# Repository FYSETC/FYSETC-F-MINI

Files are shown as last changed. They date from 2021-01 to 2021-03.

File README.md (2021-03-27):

# F-MINI

This is our open source machine: F-mini. Welcome to give us suggestions. We will keep updating this machine. You can open `F-MINI.step` file to have a 3D view. 

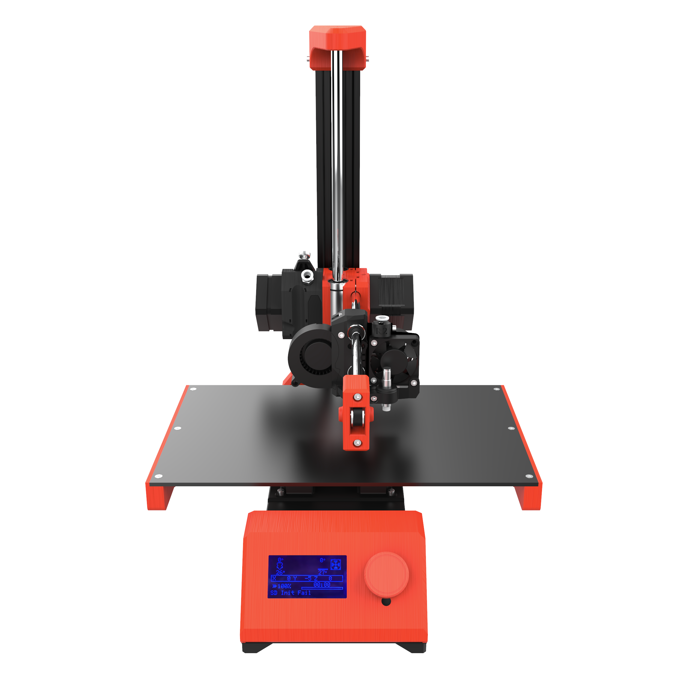
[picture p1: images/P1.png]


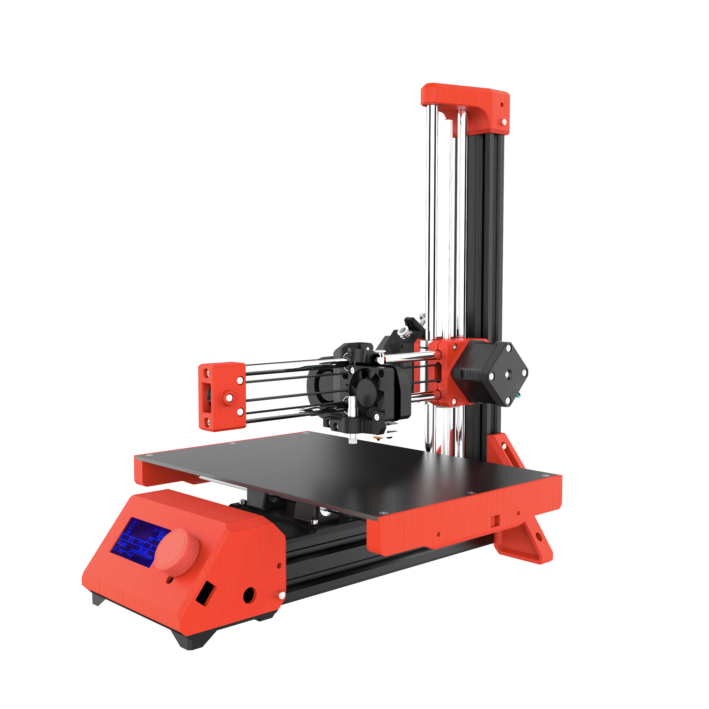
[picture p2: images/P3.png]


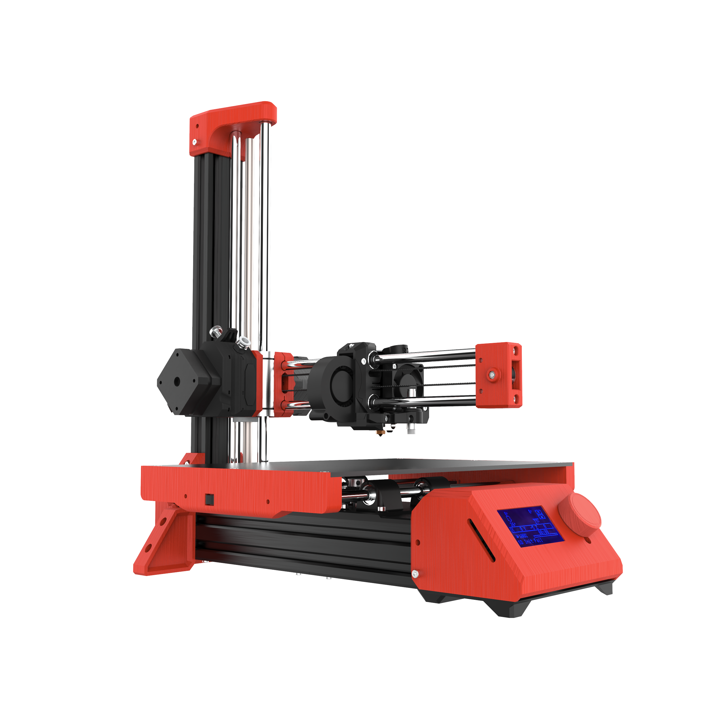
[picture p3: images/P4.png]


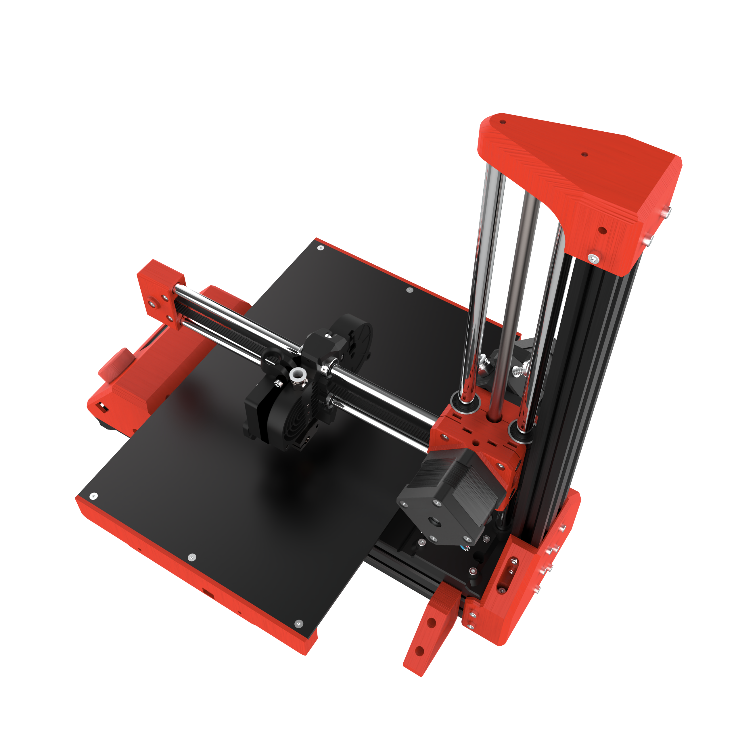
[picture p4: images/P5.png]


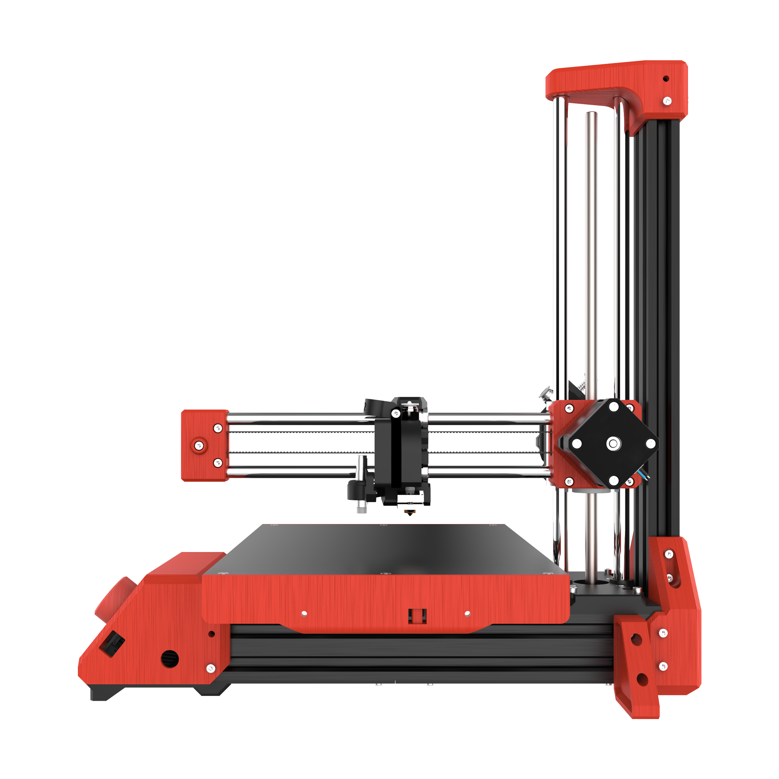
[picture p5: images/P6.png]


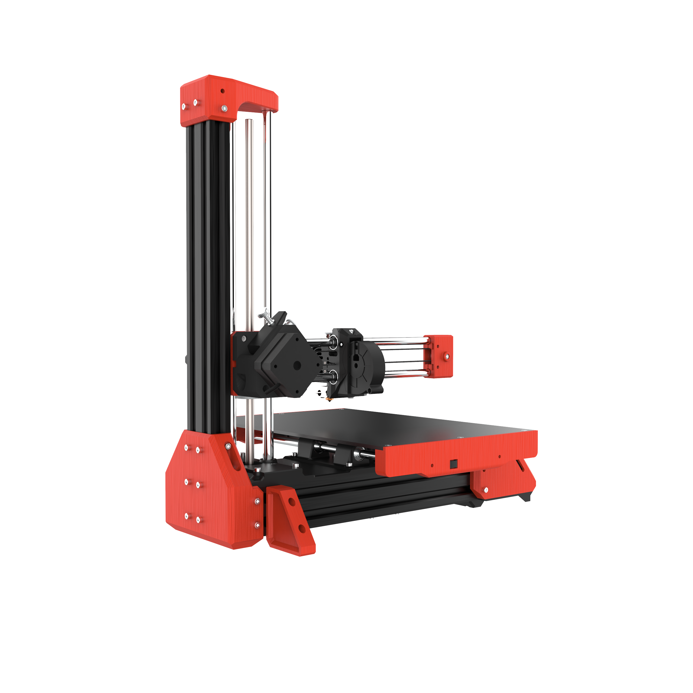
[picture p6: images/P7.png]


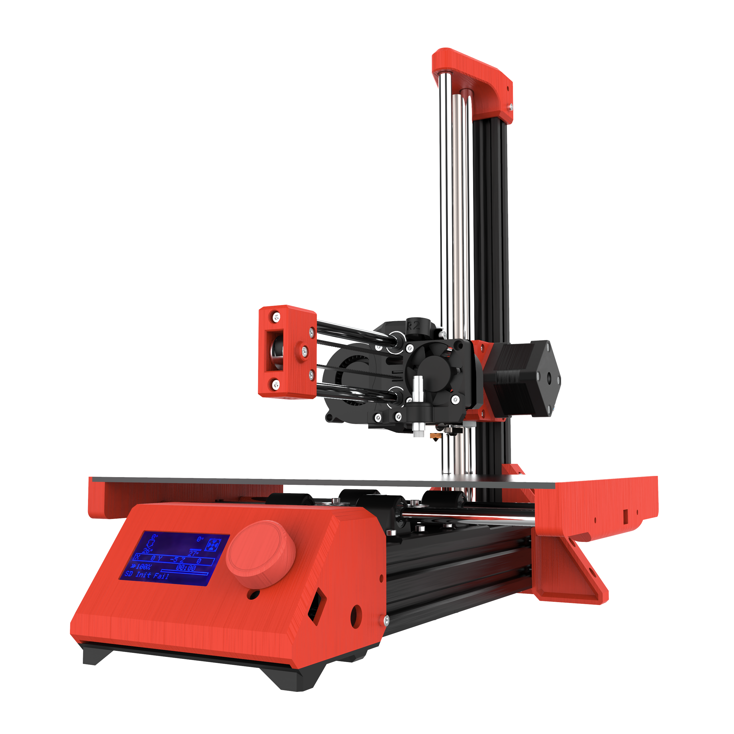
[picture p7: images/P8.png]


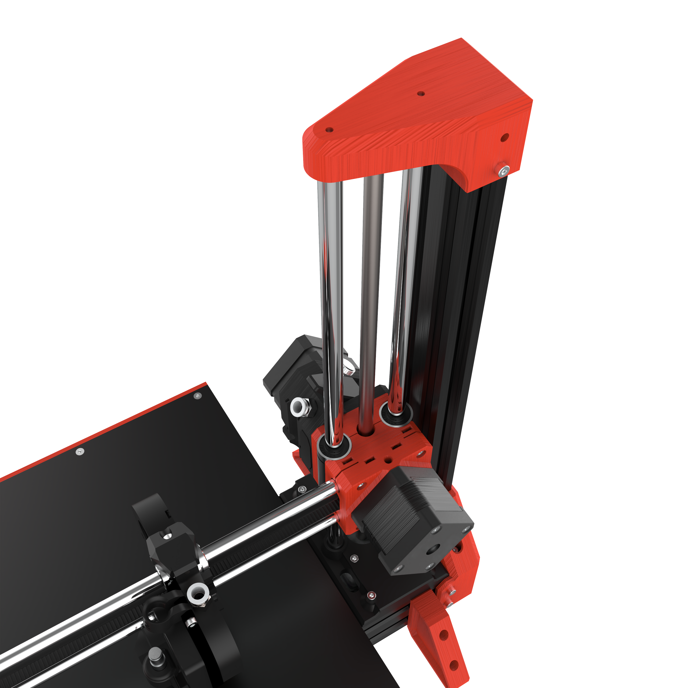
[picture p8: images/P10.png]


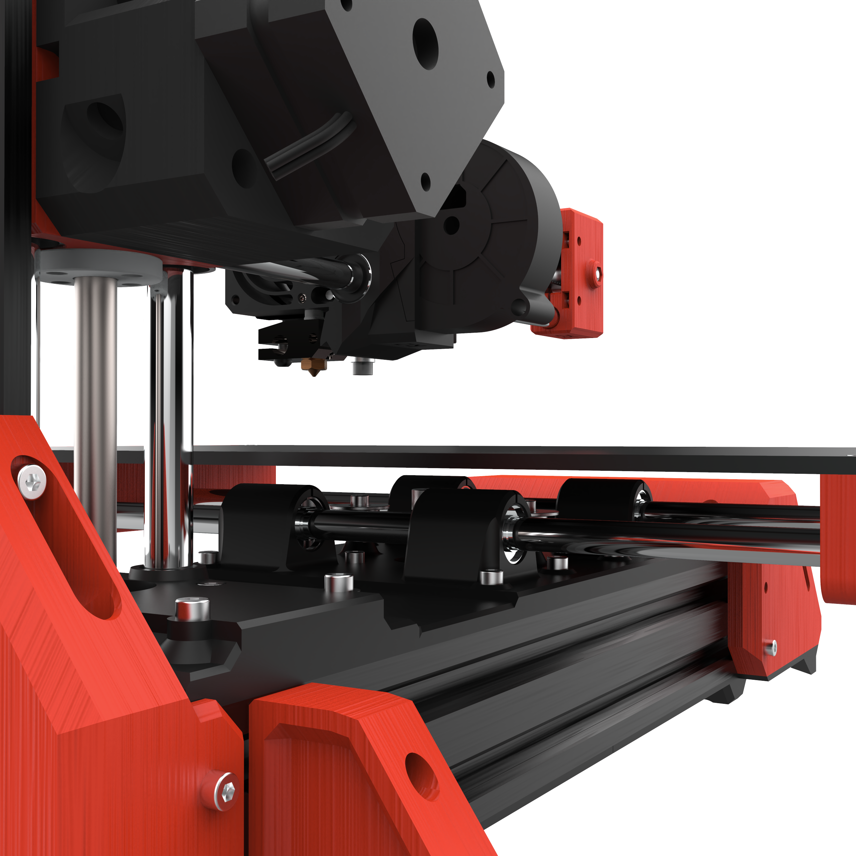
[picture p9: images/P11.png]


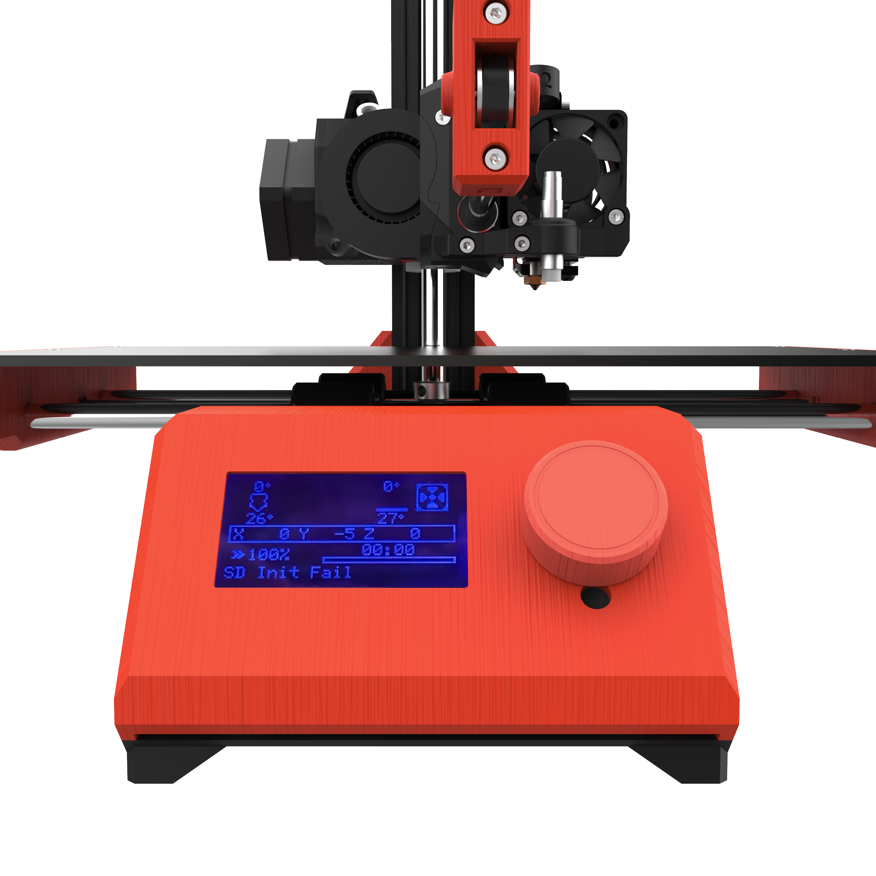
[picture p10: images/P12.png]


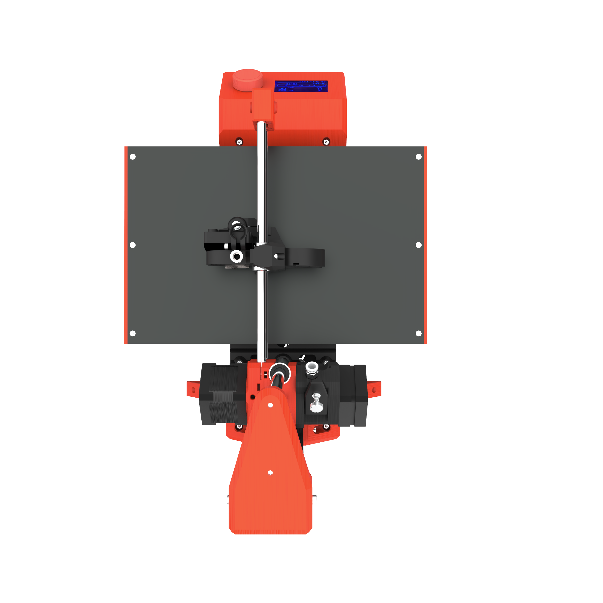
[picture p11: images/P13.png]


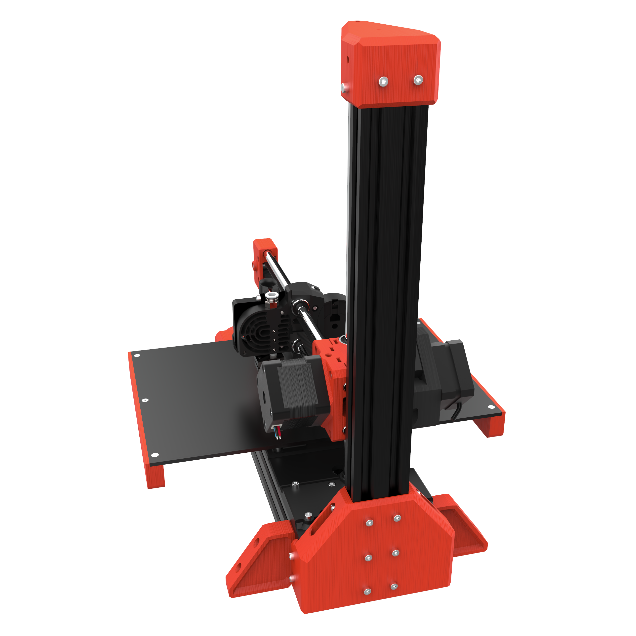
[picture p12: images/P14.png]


## Firmware

Firmware is in the `firmware` folder. Follow the `README.md` there. 

## Installation

Please follow the `installation.md` .

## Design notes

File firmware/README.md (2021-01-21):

# Firmware guide

F-MINI build with [FYSETC-AIO_II](https://github.com/FYSETC/FYSETC-AIO_II) motherboard using `Marlin` firmware.

## Marlin

### Pre-buids

There is `firmware.hex` pre-build firmware for you to test the board if you can't drive F-MINI with your own firmware.

### Build the firmware

You can follow the following steps to build the firmware your self.

#### Download Vscode + platformio

To compile the firmware , you need to install Visual Studio Code and the platformio pulg-in.

#### Download firmware

If you download already downloaded this repo, the firmware is in the ```firmware``` folder.

#### Configure the firmware

If you don't change anything of the machine, you don't need to change the configuration.

#### Compile the firmware

Open Vscode and open platformio main page and click the "Open Project" button , and direct to the folder where you put your firmware.

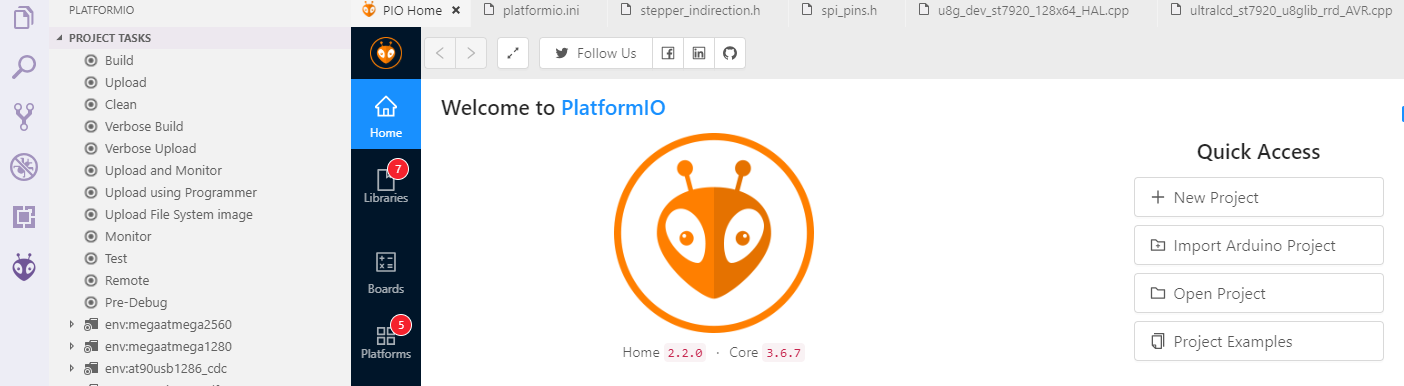
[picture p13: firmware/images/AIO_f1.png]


If everything goes fine , at the bottom you can see several buttons



Then click check mark to compile.

If you can't generate the hex file, you may need to open vscode using Administrator Account .

For more detail information，you can refer to http://marlinfw.org/docs/basics/install_platformio.html

#### Upload the firmware(windows,linux,Mac)

We provide several ways to upload the firmware .You can just click the upload button to upload the firmware or refer to the two methods below.

#### Upload the firmware(windows)

After compiling , you should see the firmware file "firmware.hex" in the folder FIRMWARE_LOCATE\Marlin\Marlin\\.pioenvs\fysetc_STM32F1\

Download the flash software in our github https://github.com/FYSETC/STM32Flasher

Connect the board and your pc with USB cable (This step should before you open the software)

Double the click "FlyMcu.exe" software to open it.

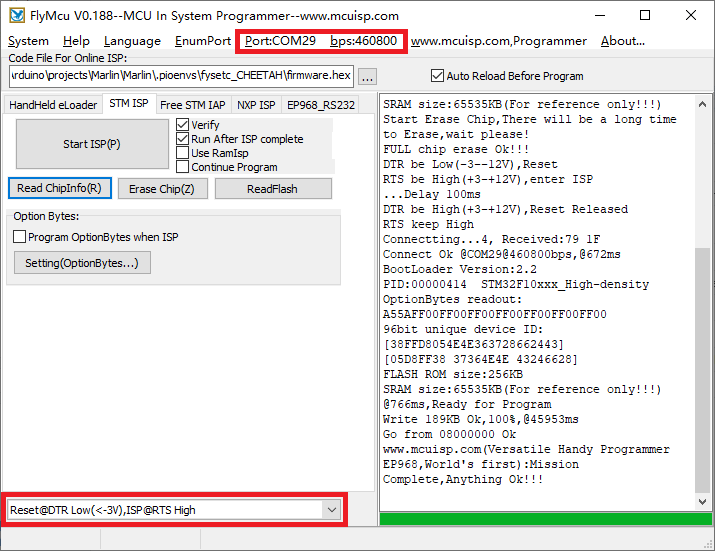
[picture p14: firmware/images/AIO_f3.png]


1. Select "***Reset@DTR low(<-3v),ISP @RTS High***"
2. Click "Port" to select the port of your USB 
3. Select ***FIRMWARE_LOCATE\Marlin\Marlin\\.pioenvs\fysetc_STM32F1\firmware.hex*** as the screenshot shows.
4. At last ,click the "Start ISP(p)" to upload the firmware.

#### Upload the firmware(linux)

##### Load usb driver

Delete the old version driver /lib/modules/$(uname -r)/kernel/drivers/usb/serial/ch341.ko

```
rm /lib/modules/$(uname -r)/kernel/drivers/usb/serial/ch341.ko
```

Download the CH34x driver(linux version) from our github

https://github.com/FYSETC/CH340-Driver

follow the readme.txt to make and load the driver .

If you want the driver load automatically every time your PC power up. You can copy the ch34x.ko file to 

directory /lib/modules/$(uname -r)/kernel/drivers/usb/serial/ , and do

```
depmod 
```

##### Install stm32flash tool

First get the code

```
git clone https://git.code.sf.net/p/stm32flash/code stm32flash-code
```

Then follow the INSTALL file to install the software

##### Upload the firmware

Connect the motherboard with USB cable and your PC. And do

```
dmesg
```

And you will get message like 



the ttyUSB0 is the port to communicate with the motherboard.

And then go the the firmware.hex file location directory and do the follow command to upload the firmware

```
 stm32flash -w firmware.hex -v -i rts,-dtr /dev/ttyUSB0
```

## Bootloader

If you want to update the firmware from sdcard, you can try this [bootloader.](https://github.com/FYSETC/Bootloader-STM32F103) Follow the README there. Or use the pre-build one in ```bootloader``` folder besides this README.

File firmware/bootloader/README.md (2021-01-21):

# Bootloader guide

You can use the sdcard to update the firmware for FYSETC-AIO_II board, you need to follow the following steps.

## Upload bootloader

You can use the bootloader hex you build or use the pre-build hex file in the OUTPUT folder.

You can use SWD , serial or USB cable. And if you are using our [Cheetah](https://github.com/FYSETC/FYSETC-Cheetah) or [AIO_II](https://github.com/FYSETC/FYSETC-AIO_II) boards , you can upload it with the STM32Flasher software which only work in Windows.

### Option 1: Upload the bootloader(windows)

There is bootloader file name ```Bootloader-STM32F103.hex``` beside this README file.

Download the flash software in our github https://github.com/FYSETC/STM32Flasher

Power the board with power supply and connect the board to your PC with USB cable (This step should before you open the software)

Double the click "FlyMcu.exe" software and open ```Bootloader-STM32F103.hex``` file.

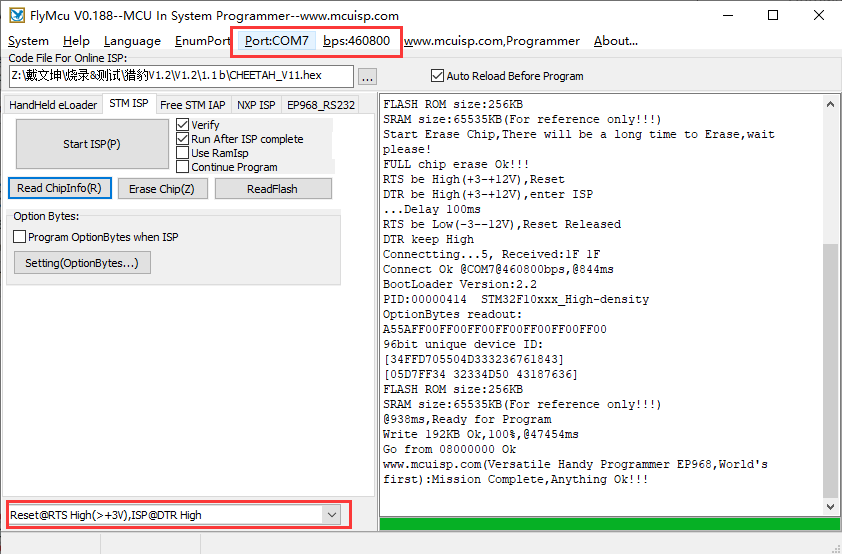
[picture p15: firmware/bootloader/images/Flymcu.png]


Select "Reset@DTR low(<-3v),ISP @RTS High"

Click "Port" to select the port of your USB 

Open Bootloader-STM32F103.hex file in the ''Code File For Online ISP:'' Editbox.

At last , "Start ISP(p)" to upload the firmware.

### Option2 : Upload the bootloader(linux)

#### Load usb driver

Delete the old version driver /lib/modules/$(uname -r)/kernel/drivers/usb/serial/ch341.ko

```
rm /lib/modules/$(uname -r)/kernel/drivers/usb/serial/ch341.ko
```

Download the CH34x driver(linux version) from our github

https://github.com/FYSETC/CH340-Driver

follow the readme.txt to make and load the driver .

If you want the driver load automatically every time your PC power up. You can copy the ch34x.ko file to 

directory /lib/modules/$(uname -r)/kernel/drivers/usb/serial/ , and do

```
depmod 
```

#### Install stm32flash tool

First get the code

```
git clone https://git.code.sf.net/p/stm32flash/code stm32flash-code
```

Then follow the INSTALL file to install the software

#### Upload the bootloader

Connect the motherboard with USB cable and your PC. And do

```
dmesg
```

And you will get message like 



the ttyUSB0 is the port to communicate with the motherboard.

And then go the the firmware.hex file location directory and do the follow command to upload the firmware

```
 stm32flash -w Bootloader-STM32F103.hex -v -i rts,-dtr /dev/ttyUSB0
```

## Rebuild firmware(Marlin)

This bootloader default boot address is 0x8010000 , so if you want to use this bootloader you need to change the firmware(I think you use Marlin, also you can use other firmware) flash address to 0x8010000.

And if you are using our stm32f103 boards([AIO_II](https://github.com/FYSETC/FYSETC-AIO_II) or [Cheetah](https://github.com/FYSETC/FYSETC-Cheetah)) . You need to add the following lines to the file "Marlin\Marlin\buildroot\share\PlatformIO\scripts\fysetc_STM32F1.py" (or check Marlin PR: https://github.com/MarlinFirmware/Marlin/pull/18179)

```
# Relocate firmware from 0x08000000 to 0x08010000
for define in env['CPPDEFINES']:
    if define[0] == "VECT_TAB_ADDR":
        env['CPPDEFINES'].remove(define)
env['CPPDEFINES'].append(("VECT_TAB_ADDR", "0x08010000"))

custom_ld_script = os.path.abspath("buildroot/share/PlatformIO/ldscripts/fysetc_stm32f103rc.ld")
for i, flag in enumerate(env["LINKFLAGS"]):
    if "-Wl,-T" in flag:
        env["LINKFLAGS"][i] = "-Wl,-T" + custom_ld_script
    elif flag == "-T":
        env["LINKFLAGS"][i + 1] = custom_ld_script
```

You can add it after the line 

```
Import("env")
```

And then rebuild the 3d printer firmware.

## Upload firmware(Marlin) with sdcard

After you upload the bootloader and rebuild the firmware(Marlin), now you can upload it to the board with sdcard

1. Copy the firmware(Marlin) to the SD card , you need to be sure the firmware name is "firmware.bin". 
2. And then power off the machine.
3. Insert the SD card to the board.
4. Power on the machine. 
5. And wait for 10~30 seconds , it will be done. 

You can connect the usb cable to monitor the process.

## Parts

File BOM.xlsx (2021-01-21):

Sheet: small 中文
模块部件 | 名称 | 规格 | 数量 | 单位 | 备注 | 参考图片 | 参考链接 | 所需紧固件明细 | 数量 | 红色备注表示已有物料
X轴模块 | X轴光轴 | 光轴直径8mm，长279mm，两端铣平，倒角C0.5 | 2 | pcs | MINI-X轴光轴 |  |  | 圆柱头内六角M3×12 | 16
 | 直线轴承 | 直线轴承LM8UU 内径8mm 外径15 高24mm 不生锈 | 2 | pcs |  |  | https://de.aliexpress.com/item/32849944212.html?spm=a2g0x.12010612.8148356.15.1f834918BBmogy | M3六角螺母 | 8
 | 直线轴承 | 直线轴承LM10LUU 内径10mm 外径19mm 高55mm 不生锈 | 2 | pcs |  |  | https://de.aliexpress.com/item/32849944212.html?spm=a2g0x.12010612.8148356.15.1f834918BBmogy | 圆柱头内六角半牙M3×25 | 6
 | 从动轮 | 20齿，内径3mm，外径12mm，高9mm，法兰厚1mm，直径18mm | 1 | pcs | 带宽6 20齿 内孔3 |  |  | M3锁紧螺母 | 2
 | 塑料卡爪 | 黑色卡爪固定4MM管 | 1 |  | miniBMG V1 |  | https://de.aliexpress.com/item/4001244491254.html | M3方形螺母 | 15
 | 卡爪夹片 | 4mm卡爪夹片 卡扣 | 1 |  |  |  |  | 圆柱头内六角半牙M3×40 | 1
 | 齿轮1.75 带机米 | 1.75-5-14-12-13.5 bondtech Gear 机米M3x2 | 1 |  |  |  |  | 圆柱头内六角半牙M3×30 | 4
 | 齿轮1.75 不带机米 | 1.75-5-14-12-13.5 bondtech Gear 不带机米 | 1 |  |  |  |  | 圆柱头内六角M3×20 | 8
 | 电机齿轮 带机米 | 5-13-9.5 bondtech Gear 机米M3x2 | 1 |  |  |  |  | 半圆头内六角M3×10 | 1
 | 塑料齿轮 | 模数0.5 50齿 压力角20 内径5mm 宽7.3mm POM | 1 |  |  |  |  | 机米螺丝M3×4 | 8
 | 滚针轴承 | K357 内径3mm 外径5mm 高7mm | 2 |  |  |  |  | 机米螺丝M3×2 | 1
 | 滚珠轴承 | MR85ZZ 内径5mm 外径8mm 高2.5mm | 2 |  |  |  |  | 圆柱头内六角M3X6 | 1
 | 齿轮轴 | 直径5mm齿轮轴 | 1 |  |  |  |  | 圆柱头内六角M3X35 | 4
 | 销钉 | 实心圆柱销φ3X20mm | 1
 | 销钉 | 实心圆柱销φ3X30mm | 1
 | 手拧螺钉 | 滚花不锈钢平头手拧螺丝M3X20 | 1
 | 弹簧 | 弹簧 线径1.2 外径6 长10mm | 1
 | 垫片 | M3垫片 内径3.2mm 外径7mm 厚度0.5mm | 1
 | 快插接头 | 直通式快插接头 PC04-01 | 1
 | 42步进电机 | 高40mm，长42mm，宽42mm，电机线长度800mm | 2 | pcs |  |  | https://de.aliexpress.com/item/32962573026.html?spm=a2g0x.12010612.8148356.15.a0c31d08HBK7uh
 | 同步带 | 2GT-6 开口带 L（560）mm 带宽6mm 齿距2mm | 1 | pcs |  |  | https://de.aliexpress.com/item/4000074170302.html?spm=a2g0x.12010612.8148356.49.38fdaef8N1sKo4
 | 同步轮 | 2GT 16齿，内孔5，带机米螺丝 | 1 | pcs | prusa 同款
 | 涡轮冷料风扇 | 5010 24V涡轮鼓风机风扇 4000转 线长1200 不需要套管 | 1 | pcs | 原5V
 | 散热风扇 | 4010 24V挤出机散热风扇 5000转 线长1200 不需要套管 | 1 | pcs | 原5V |  | https://de.aliexpress.com/item/33017502840.html?spm=a2g0x.12010612.8148356.5.38fdaef8N1sKo4
 | 调平开关 | 接近开关，直径8mm 线长1200mm 电压4-35v 三线4pin | 1 | pcs
 | 挤出头散热器 | prusa mini挤出头散热器 | 1 | pcs | PRMINI-M02
 | 喉管 | prusa mini喉管 | 1 | pcs | PRMINI-M04
 | 加热块 | E3D V6新款加热块 PT100 | 1 | pcs |  |  | https://de.aliexpress.com/item/32898958070.html?spm=a2g0x.12010612.8148356.21.21e748f3ur5pdn
 | 硅胶套 | E3D V6新款加热块PT100 硅胶套 颜色随机 | 1 | pcs
 | 喷嘴 | E3D V6喷嘴 0.4mm 刻字 | 1 | pcs |  |  | https://de.aliexpress.com/item/32922218908.html?spm=a2g0x.12010612.8148356.69.21e748f3syPCVT
 | 快插接头 | PC-01快插接头 直通 | 2 | pcs
 | 加热棒 | 24V 40W 直径6mm 长度15mm 线长1200mm | 1 | pcs
 | 测温线 | 带壳热敏电阻 线长1200 | 1 | pcs
 | 铁氟龙管 | 内径1.9 外径4 蓝色铁氟龙管 长度150 | 1 | pcs
 | 铁氟龙管 | 内径1.9 外径4 蓝色铁氟龙管 要求两端端面非常平 长度300 | 1 | pcs
 | 线束套管 | 自卷式纺织套管 5mm 长300 | 1 | pcs
 | 线束套管 | 自卷式纺织套管 10mm 长720 | 1 | pcs
模块部件 | 名称 | 规格 | 数量 | 单位 | 备注 | 参考图片 | 参考链接 | 所需紧固件明细 | 数量
Y轴模块 | Y轴型材 | 20*40型材，长302mm | 2 | pcs | MINI-Y轴型材302 |  |  | 圆柱头内六角M3×12 | 8
 | Y轴光杆 | 光轴直径8mm，长284mm，两端铣平，倒角C0.5 | 2 | pcs | MINI-Y轴光轴 |  |  | 内花角平头螺钉M3×2 | 9
 | 42步进电机 | 高40mm，长42mm，宽42mm，电机线长度220mm | 1 | pcs |  |  | https://de.aliexpress.com/item/32962573026.html?spm=a2g0x.12010612.8148356.15.a0c31d08HBK7uh | M3锁紧螺母 | 12
 | 同步轮 | 2GT 16齿，内孔5，带机米螺丝 | 1 | pcs | prusa 同款 |  |  | 圆柱头内六角M3×8 | 15
 | 线束套管 | 自卷式纺织套管 5mm 长350 | 1 | pcs |  |  |  | 圆柱头内六角螺栓M3×20 | 3
 | 直线轴承 | 直线轴承LM8UU 内径8mm 外径15 高24mm 不生锈 | 4 | pcs |  |  | https://de.aliexpress.com/item/32849944212.html?spm=a2g0x.12010612.8148356.15.1f834918BBmogy
 | 从动轮 | 20齿，内径3mm，外径12mm，高9mm，法兰厚1mm直径18mm | 2 | pcs | 带宽6 20齿 内孔3
 | 同步带 | 2GT-6 开口带 L（350）mm 带宽6mm 齿距2mm | 1 | pcs |  |  | https://de.aliexpress.com/item/4000074170302.html?spm=a2g0x.12010612.8148356.49.38fdaef8N1sKo4
模块部件 | 名称 | 规格 | 数量 | 单位 | 备注 | 参考图片 | 参考链接 | 所需紧固件明细 | 数量
Z轴模块 | Z轴型材 | 20*40型材，长380mm | 1 | pcs | MINI-Z轴型材380 |  |  | 圆柱头内六角M3×8 | 8
 | Z轴光杆 | 光轴直径10mm，长340mm，两端铣平，倒角C0.5 | 2 | pcs | MINI-Z轴光轴 |  |  | M3六角螺母 | 8
 | 42步进电机（带丝杆+电机线） | 电机高34mm 长42mm 宽42mm；梯形丝杆直径8mm 螺距2mm 2头导程4mm 长度310mm，电机线长度500mm 配POM螺母T8 导程4 螺距2 | 1 | pcs |  |  |  | M3方形螺母 | 10
模块部件 | 名称 | 规格 | 数量 | 单位 | 备注 | 参考图片 | 参考链接 | 所需紧固件明细 | 数量
其他部件 | 电源 | 暂没确定 | 1 | 1 |  |  |  | T型螺母 M3 | 50
 | AIO显示屏 |  | 1 | 1 |  |  | https://de.aliexpress.com/item/33042243225.html?spm=a2g0x.12010615.8148356.5.61ed53cec7Wrg6 | 圆柱头内六角M3×14 | 10
 | 热床 | 按图定制 线长500mm | 1 | 1
 | 打印件 | 按图纸打印

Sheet: small bom
Module parts | designation | specification | qty | unit | remarks | reference picture | reference linking | fastener | Quantity
X axis module | X axis optical axis | The diameter of the optical axis is 8mm, the length is 279mm, both ends are milled, and the chamfer is C0.5 | 2 | pcs | MINI-X axis optical axis |  |  | M3×12 SHCS | 16
 | linear bearing | Linear bearing LM8UU inner diameter 8mm outer diameter 15 height 24mm | 2 | pcs |  |  | https://de.aliexpress.com/item/32849944212.html?spm=a2g0x.12010612.8148356.15.1f834918BBmogy | M3 Hexnut | 8
 | linear bearing | Linear bearing LM10LUU inner diameter 10mm outer diameter 19mm high 55mm | 2 | pcs |  |  | https://de.aliexpress.com/item/32849944212.html?spm=a2g0x.12010612.8148356.15.1f834918BBmogy | M3×25 SHCS | 6
 | driven pulley | 20 teeth, inner diameter 3mm, outer diameter 12mm, high 9mm, flange thickness 1mm, diameter 18mm | 1 | pcs | Bandwidth 6 20 tooth inner hole 3 |  |  | M3 locknut | 2
 | Plastic jaw | Black claw fixed 4MM tube | 1 |  | miniBMG V1 |  | https://de.aliexpress.com/item/4001244491254.html | M3 square nut | 15
 | Jaw clamping piece | 4mm claw clip buckle | 1 |  |  |  |  | M3×40 SHCS | 1
 | Gear 1.75 belt machine meters | 1.75-5-14-12-13.5 bondtech Gear M3x2 grub screw | 1 |  |  |  |  | M3×30 SHCS | 4
 | Gear 1.75 without machine meter | 1.75-5-14-12-13.5 bondtech Gear No machine m | 1 |  |  |  |  | M3×20 SHCS | 8
 | Motor gear belt machine meters | 5-13-9.5 bondtech Gear M3x2 grub screw | 1 |  |  |  |  | M3×10 BHCS | 1
 | plastic gear | Modulus 0.5 50 tooth pressure Angle 20 inner diameter 5mm width 7.3mm POM | 1 |  |  |  |  | M3×4 grub screw | 8
 | ball bearing | K357 inner diameter 3mm outer diameter 5mm high 7mm | 2 |  |  |  |  | M3×2 grub screw | 1
 | ball bearing | MR85ZZ inner diameter 5mm outer diameter 8mm high 2.5mm | 2 |  |  |  |  | M3X6 SHCS | 1
 | gear shaft | Diameter 5mm gear shaft | 1 |  |  |  |  | M3X35 SHCS | 4
 | pin bolt | Solid cylindrical pin Φ3x20mm | 1
 | pin bolt | Solid cylindrical pin Φ3x20mm | 1
 | hand screw | Knurled stainless steel flat head hand screw M3X20 | 1
 | spring | Spring wire diameter 1.2 outside diameter 6 long 10mm | 1
 | spacer | M3 gasket inner diameter 3.2mm outer diameter 7mm thickness 0.5mm | 1
 | quick connector | Straight-through quick plug connector PC04-01 | 1
 | 42 Stepper motor | Height 40mm, length 42mm, width 42mm, motor line length 800mm | 2 | pcs |  |  | https://de.aliexpress.com/item/32962573026.html?spm=a2g0x.12010612.8148356.15.a0c31d08HBK7uh
 | synchronous belt | 2GT-6 opening with L (560) mm bandwidth 6mm pitch 2mm | 1 | pcs |  |  | https://de.aliexpress.com/item/4000074170302.html?spm=a2g0x.12010612.8148356.49.38fdaef8N1sKo4
 | synchronizing wheel | 2GT 16 teeth, inner hole 5, with machine screw | 1 | pcs
 | Turbine cold feed fan | 5010 24V turbo blower fan 4000 RPM line length 1200 no casing required | 1 | pcs
 | cooling fan | 4010 24V extruder cooling fan 5000 RPM wire length 1200 no casing required | 1 | pcs |  |  | https://de.aliexpress.com/item/33017502840.html?spm=a2g0x.12010612.8148356.5.38fdaef8N1sKo4
 | The level switch | Proximity switch, diameter 8mm line length 1200mm voltage 4-35V three wire 4pin | 1 | pcs
 | Extruder radiator | prusa mini extruder head radiator | 1 | pcs | PRMINI-M02
 | hotend heat break | prusa mini hotend heat break | 1 | pcs | PRMINI-M04
 | heat block | E3D V6 new heating block PT100 | 1 | pcs |  |  | https://de.aliexpress.com/item/32898958070.html?spm=a2g0x.12010612.8148356.21.21e748f3ur5pdn
 | silicon rubber case | E3D V6 new heating block PT100 silica gel sleeve color random | 1 | pcs
 | nozzle | E3D V6 nozzle 0.4mm lettering | 1 | pcs |  |  | https://de.aliexpress.com/item/32922218908.html?spm=a2g0x.12010612.8148356.69.21e748f3syPCVT
 | quick connector | PC-01 quick plug connector through | 2 | pcs
 | heating rod | 24V 40W diameter 6mm length 15mm line length 1200mm | 1 | pcs
 | Temperature measurement line | Shell thermistor wire length 1200mm | 1 | pcs
 | teflon tube | Inner diameter 1.9 outer diameter 4 blue Teflon tube length 150mm | 1 | pcs
 | teflon tube | The inner diameter is 1.9 and the outer diameter is 4. The blue Teflon tube is required to have very flat ends and the length is 300mm | 1 | pcs
 | Wiring harness casing | Self-winding textile sleeve 5mm long 300mm | 1 | pcs
 | Wiring harness casing | Self-winding textile sleeve 10mm long 720mm | 1 | pcs
Module parts | designation | specification | quantity | unit | remarks | reference picture | reference linking | fastener | Quantity
Y axis module | Y profile | 20*40 profiles, length 302mm | 2 | pcs | Mini-Y axis profile 302mm |  |  | M3×12 SHCS | 8
 | Y polished rod | The optical axis diameter is 8mm, length is 284mm, both ends are milling flat, chamfering is C0.5 | 2 | pcs | The MINI - Y axis |  |  | M3×2 Flat head screws with inner corner | 9
 | 42 Stepper motor | High 40mm, length 42mm, width 42mm, motor line length 220mm | 1 | pcs |  |  | https://de.aliexpress.com/item/32962573026.html?spm=a2g0x.12010612.8148356.15.a0c31d08HBK7uh | M3 locknut | 12
 | synchronizing wheel | 2GT 16 teeth, inner hole 5, with machine screw | 1 | pcs | Prusa with money |  |  | M3×8 SHCS | 15
 | Wiring harness casing | Self-winding textile casing 5mm long 350 | 1 | pcs |  |  |  | M3×20 SHCS | 3
 | linear bearing | Linear bearing LM8UU inner diameter 8mm outer diameter 15 height 24mm | 4 | pcs |  |  | https://de.aliexpress.com/item/32849944212.html?spm=a2g0x.12010612.8148356.15.1f834918BBmogy
 | driven pulley | 20 teeth, inner diameter 3mm, outer diameter 12mm, high 9mm, flange thickness 1mm diameter 18mm | 2 | pcs | Bandwidth 6mm 20 tooth inner hole 3mm
 | synchronous belt | 2GT-6 opening with L (350) mm bandwidth 6mm pitch 2mm | 1 | pcs |  |  | https://de.aliexpress.com/item/4000074170302.html?spm=a2g0x.12010612.8148356.49.38fdaef8N1sKo4
Module parts | designation | specification | quantity | unit | remarks | reference picture | reference linking | fastener | Quantity
Z axis module | Z axis profile | 20*40 profiles, 380mm long | 1 | pcs | Mini-Z axis profile 380mm |  |  | M3×8 SHCS | 8
 | Z axis polished rod | Optical axis diameter 10mm, length 340mm, both ends milling flat, chamfering C0.5 | 2 | pcs | MINI - Z axis axis |  |  | M3 Hexnut | 8
 | 42 Stepper motor (with screw + motor wire) | Motor height 34mm long 42mm wide 42mm;Trapezoidal lead screw diameter 8mm pitch 2mm 2 lead 4mm length 310mm, motor wire length 500mm with POM nut T8 lead 4 pitch 2 | 1 | pcs |  |  |  | M3 square nut | 10
Module parts | designation | specification | quantity | unit | remarks | reference picture | reference linking | fastener | Quantity
miscellaneous part | power supply | 24V | 1 | 1 |  |  |  | M3 Hammer Head T-nuts | 50
 | AIO display |  | 1 | 1 |  |  | https://de.aliexpress.com/item/33042243225.html?spm=a2g0x.12010615.8148356.5.61ed53cec7Wrg6 | M3×14 SHCS | 10
 | Hot bed | The line length is 500mm according to the drawing | 1 | 1
 | printed matter | Print to drawing

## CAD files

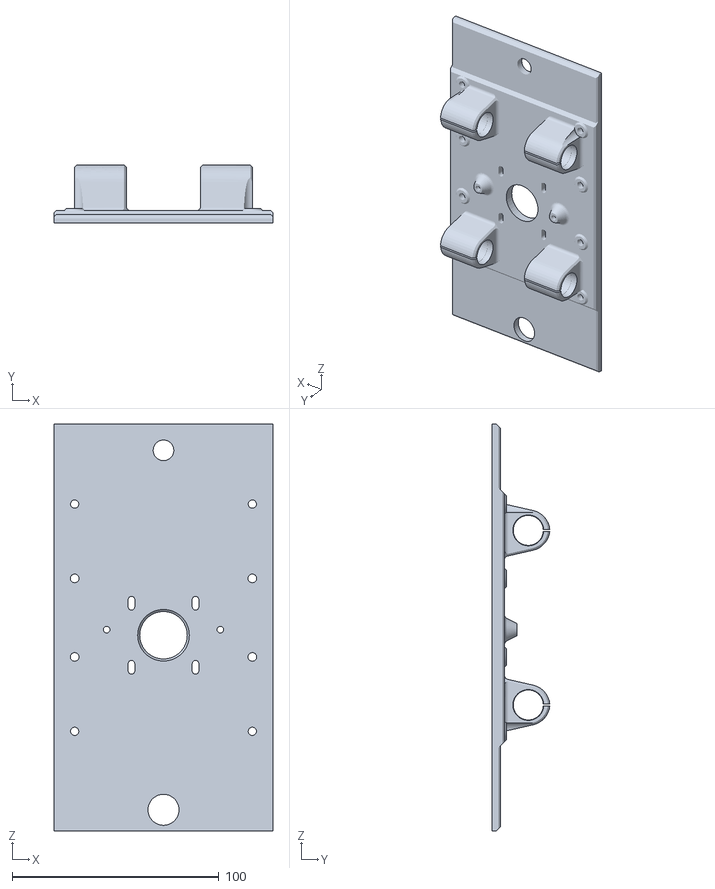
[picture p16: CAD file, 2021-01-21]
STLs/black/Y axis motor fixing plate.STL
106.0 x 27.9 x 197.0

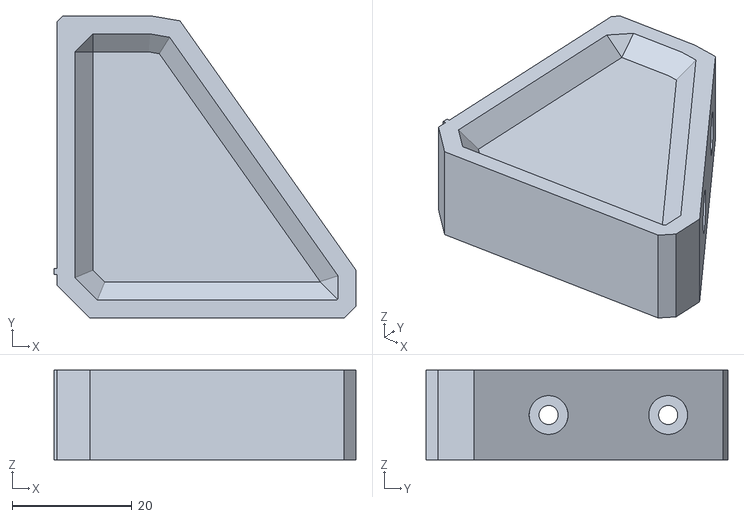
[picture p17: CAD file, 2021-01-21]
STLs/red/Strengthen the horse X2.STL
50.5 x 50.5 x 15.0

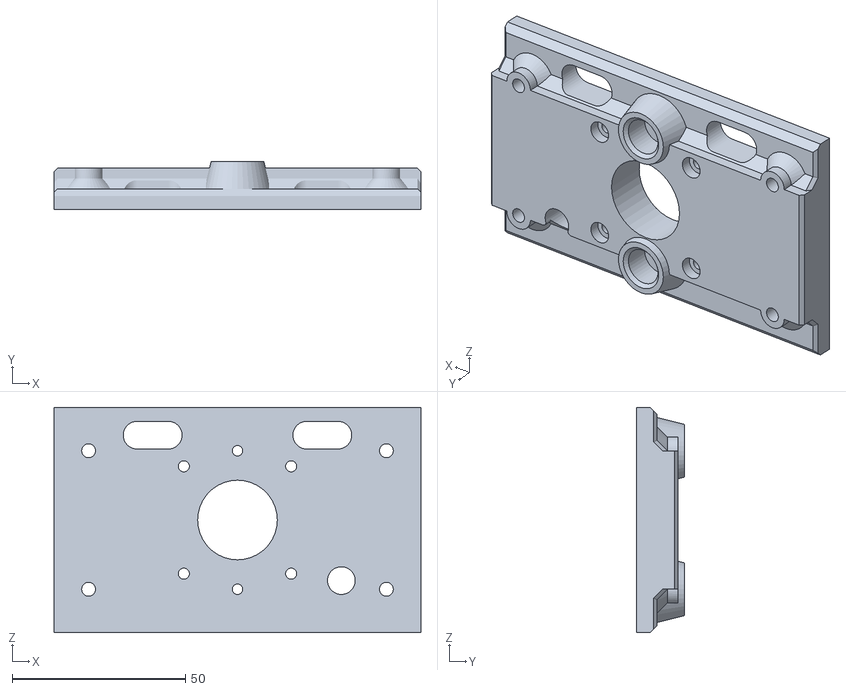
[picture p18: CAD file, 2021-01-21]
STLs/black/Z axis motor fixing plate.STL
106.0 x 14.0 x 65.0

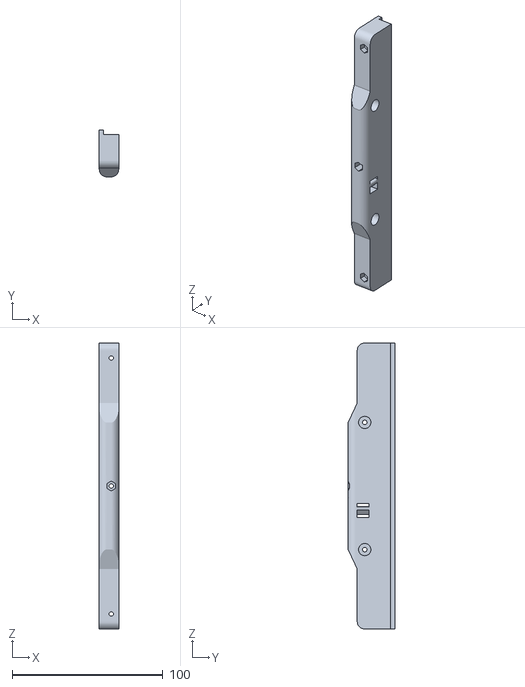
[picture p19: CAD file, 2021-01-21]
STLs/red/Mirror to AIO 180 hot bed support.STL
13.0 x 31.0 x 190.0

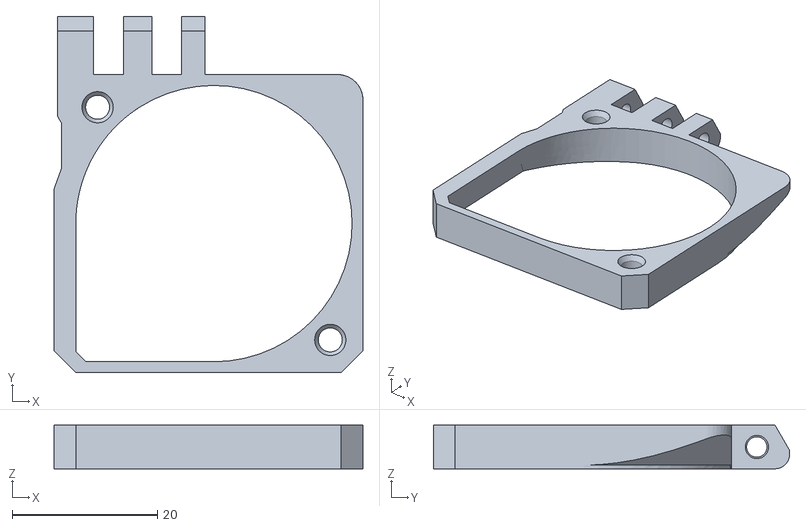
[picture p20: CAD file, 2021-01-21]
STLs/black/MINI-fan-spacer.STL
42.5 x 49.0 x 6.00

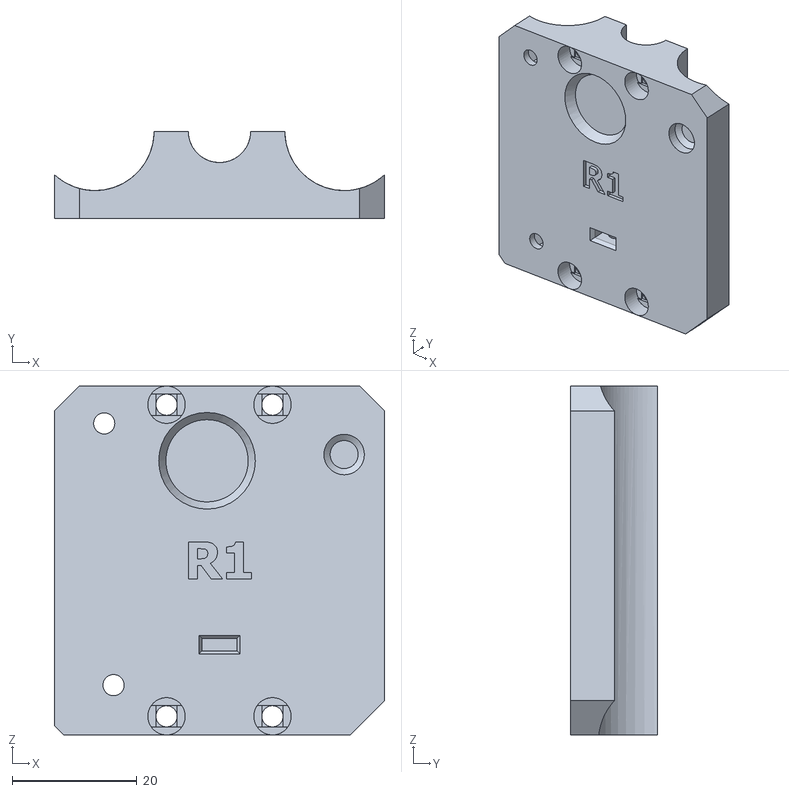
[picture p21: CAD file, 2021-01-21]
STLs/red/MINI-z-carriage-rear.STL
53.0 x 14.0 x 56.0

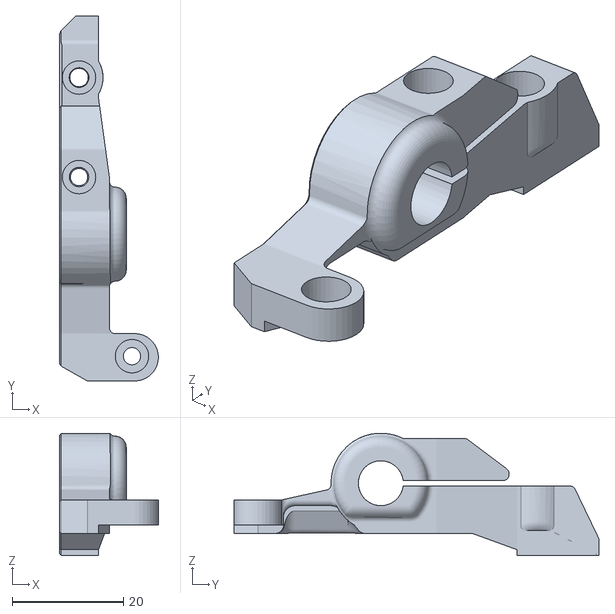
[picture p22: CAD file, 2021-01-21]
STLs/black/MINI-minda-holder.STL
17.8 x 65.5 x 22.0

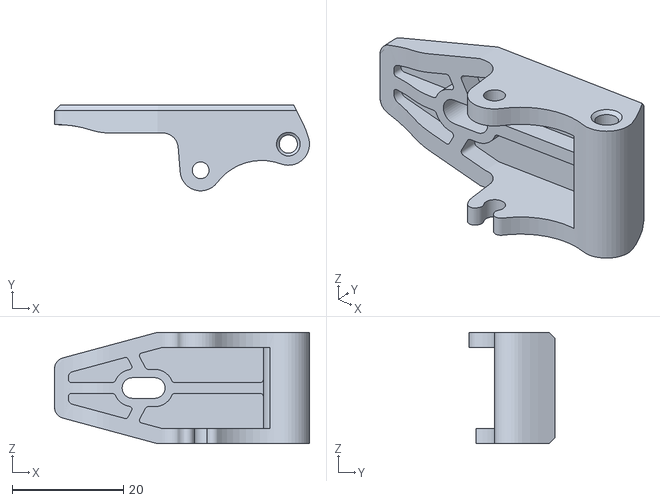
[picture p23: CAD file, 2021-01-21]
STLs/red/Bondtech BMG pressure lever.STL
45.8 x 15.4 x 20.0

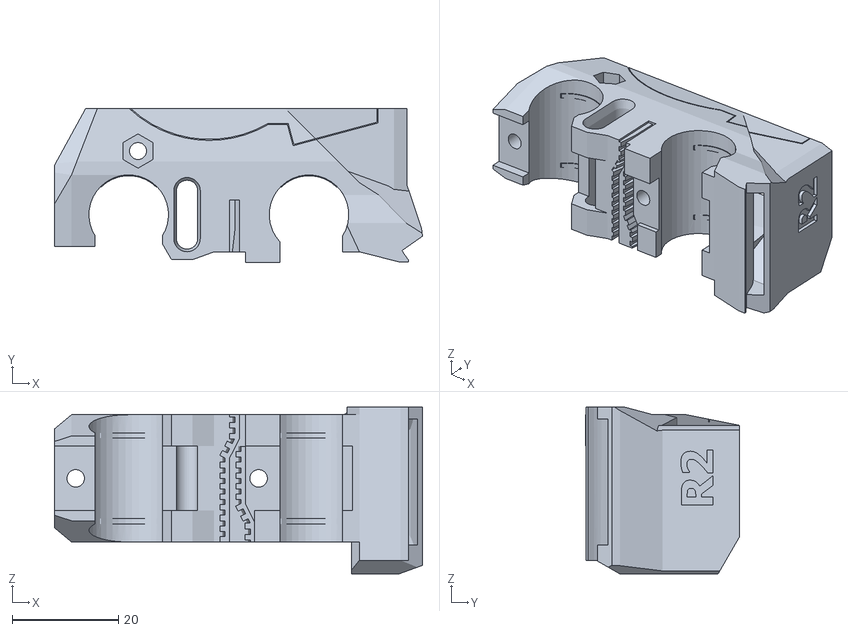
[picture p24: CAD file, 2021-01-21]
STLs/black/MINI-x-carriage.STL
69.4 x 29.0 x 31.4

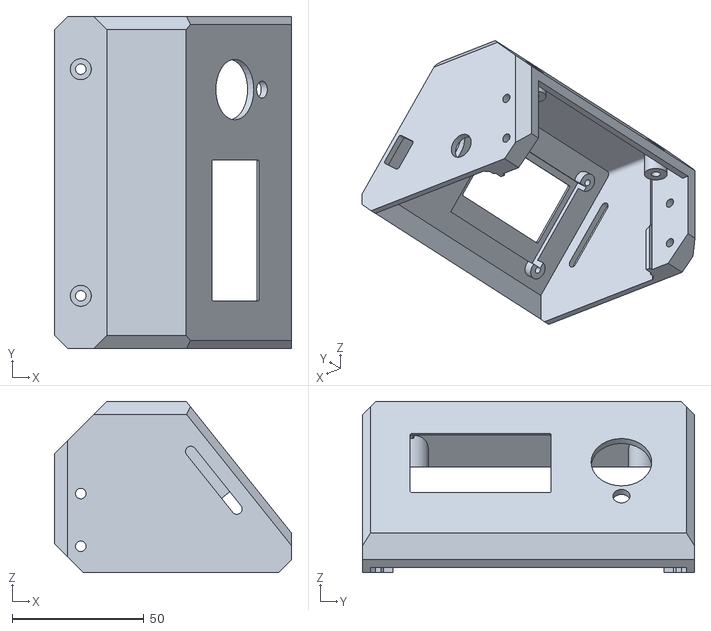
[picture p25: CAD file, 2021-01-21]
STLs/red/Front Case-3-2.STL
90.0 x 126.0 x 65.0

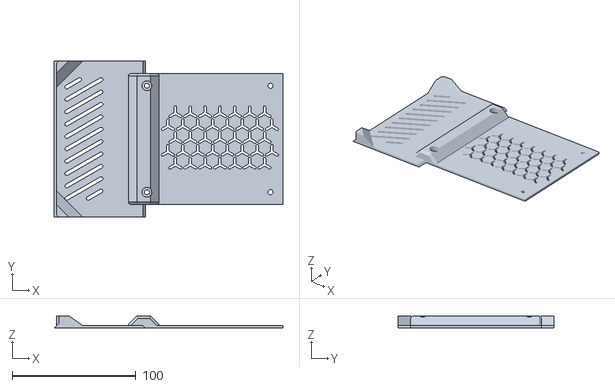
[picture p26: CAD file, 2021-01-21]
STLs/black/Floor 3.STL
185.0 x 126.0 x 10.0

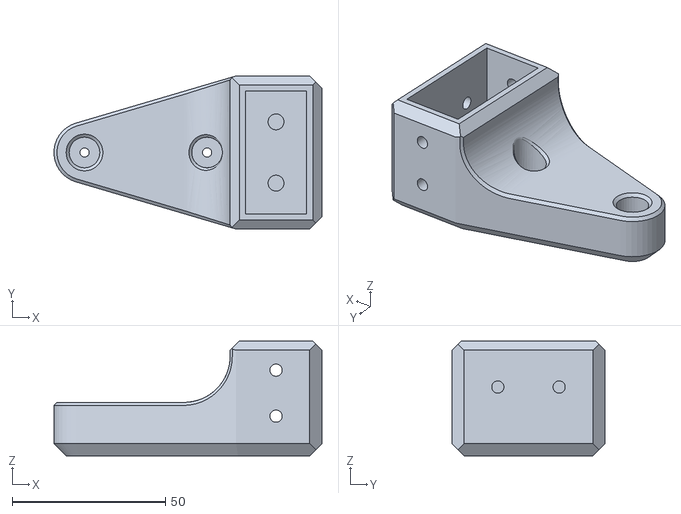
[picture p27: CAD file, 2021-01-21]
STLs/red/Z-top.STL
87.5 x 50.0 x 37.5

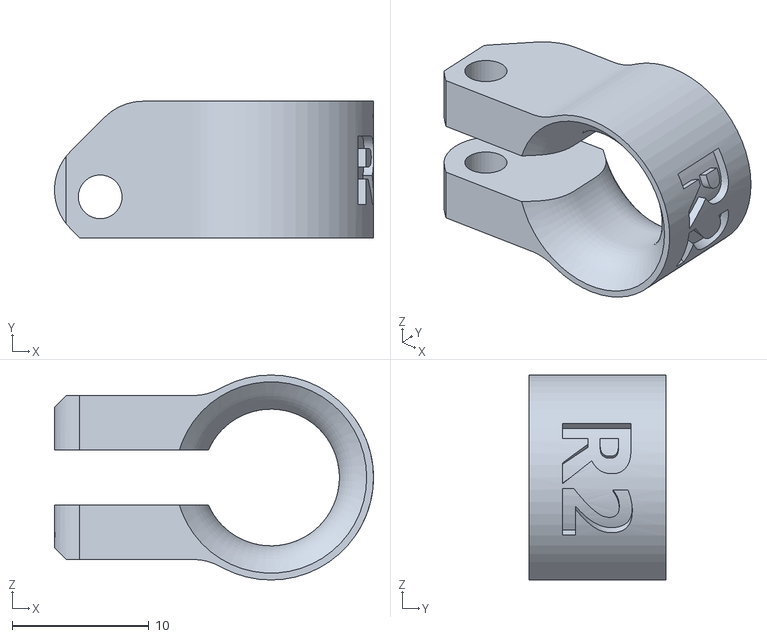
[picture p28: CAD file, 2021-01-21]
STLs/black/MINI-fan-spacer-clip.STL
23.3 x 10.00 x 15.0

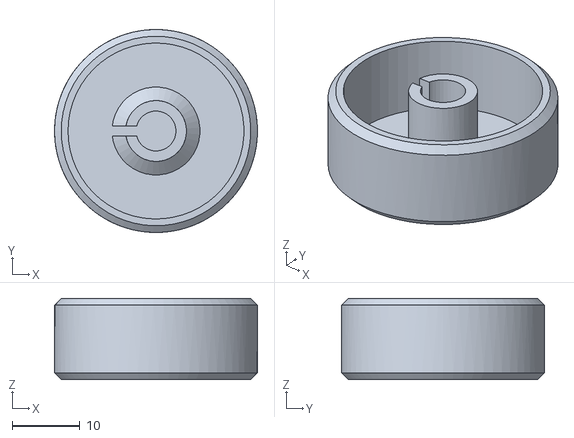
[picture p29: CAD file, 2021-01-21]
STLs/black/knob.STL
30.0 x 30.0 x 12.0

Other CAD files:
STLs/red/AIO 180 hot bed support.STL
STLs/red/MINI-x-end.STL
STLs/black/Floor 1.STL
STLs/red/Z-axis profile fixator.STL
STLs/red/BMG bottom case.STL
STLs/red/BMG outer shell .STL
STLs/red/MINI-z-carriage-front.STL

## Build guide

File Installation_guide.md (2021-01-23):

## Installation

You need to follow the following steps to build this machine.

1. Print all the STL files in `STLs` folder.
2. Get all the parts in BOM file.
3. Follow the steps bellow to build.

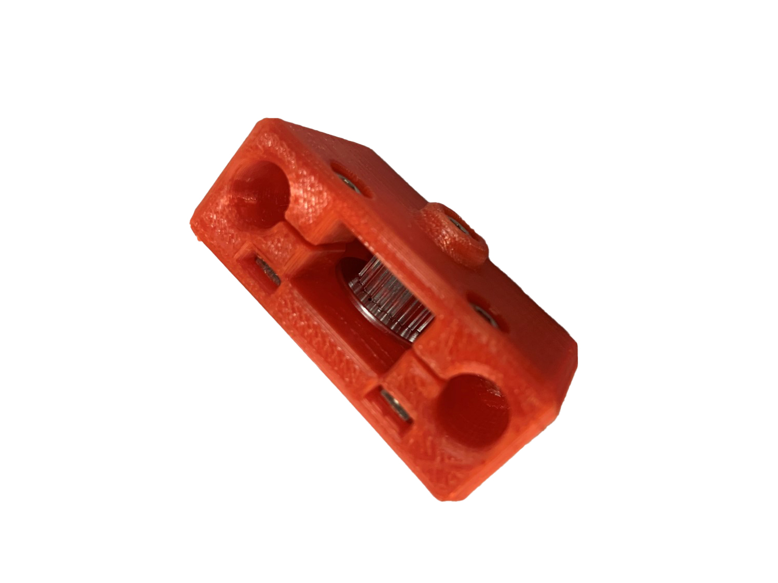
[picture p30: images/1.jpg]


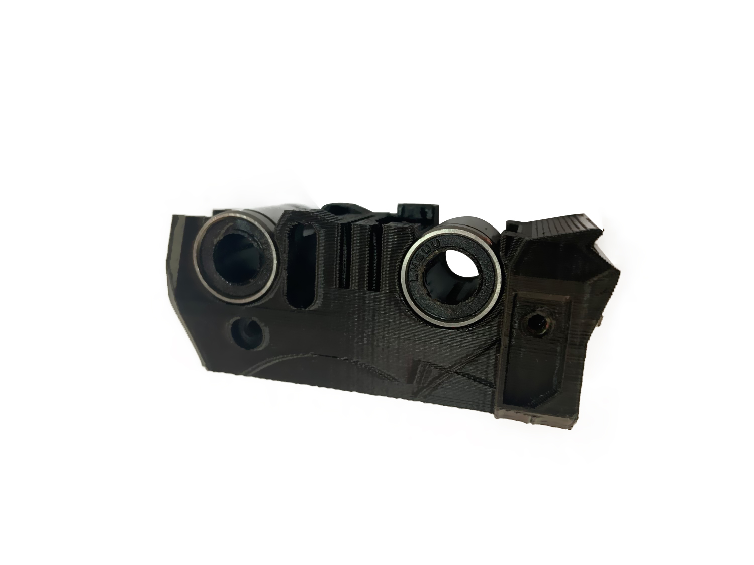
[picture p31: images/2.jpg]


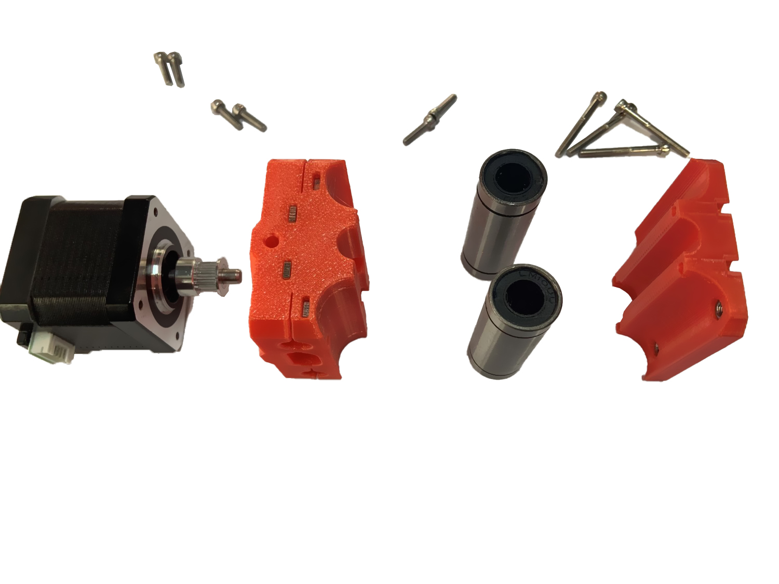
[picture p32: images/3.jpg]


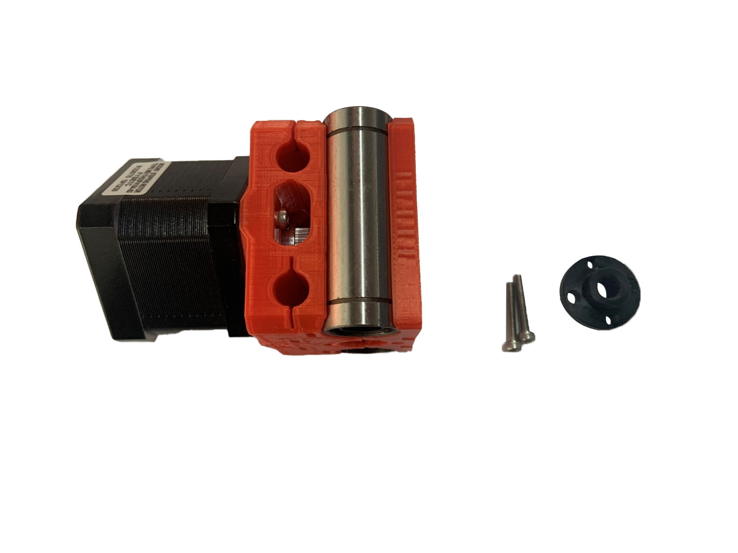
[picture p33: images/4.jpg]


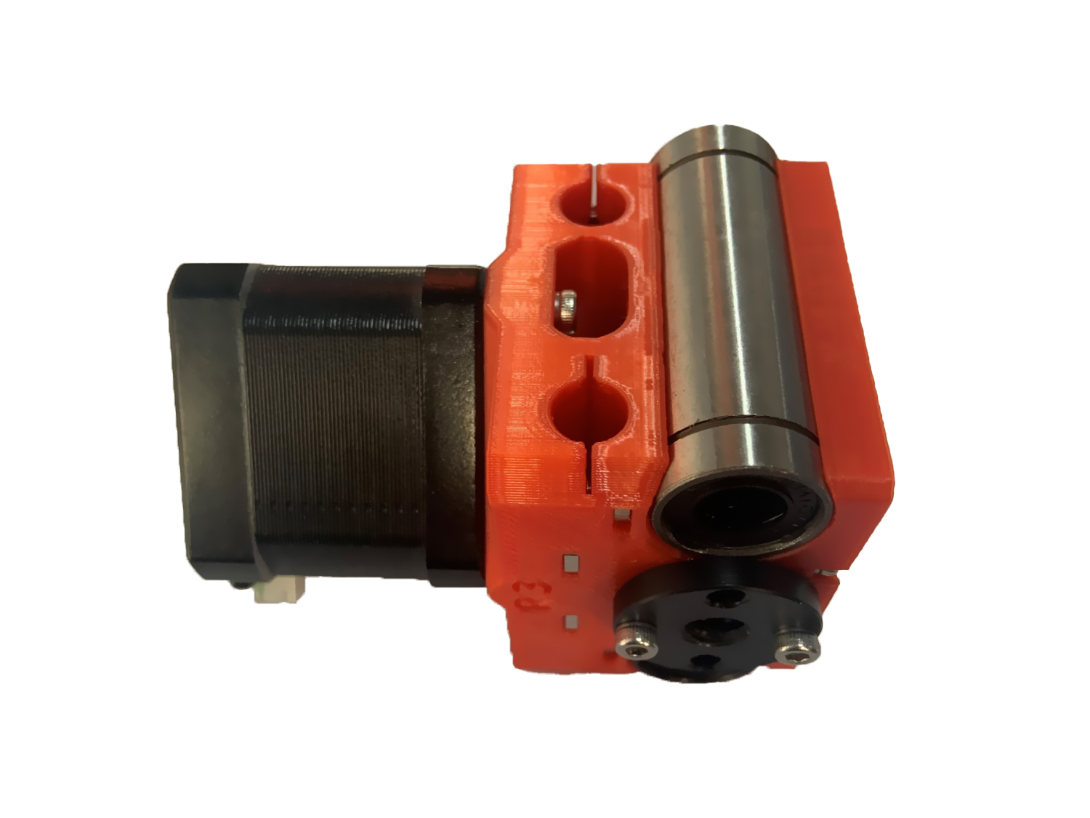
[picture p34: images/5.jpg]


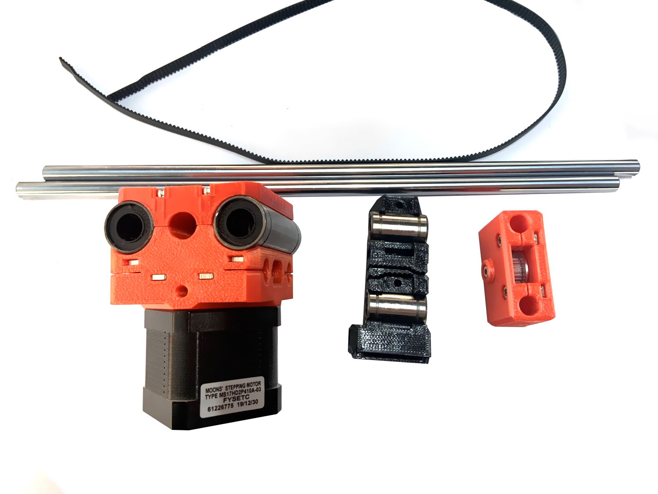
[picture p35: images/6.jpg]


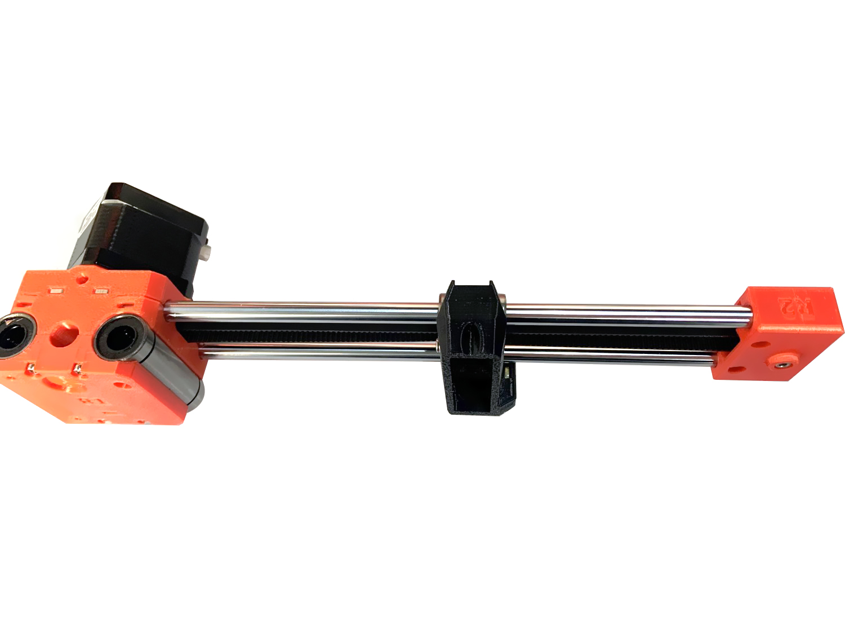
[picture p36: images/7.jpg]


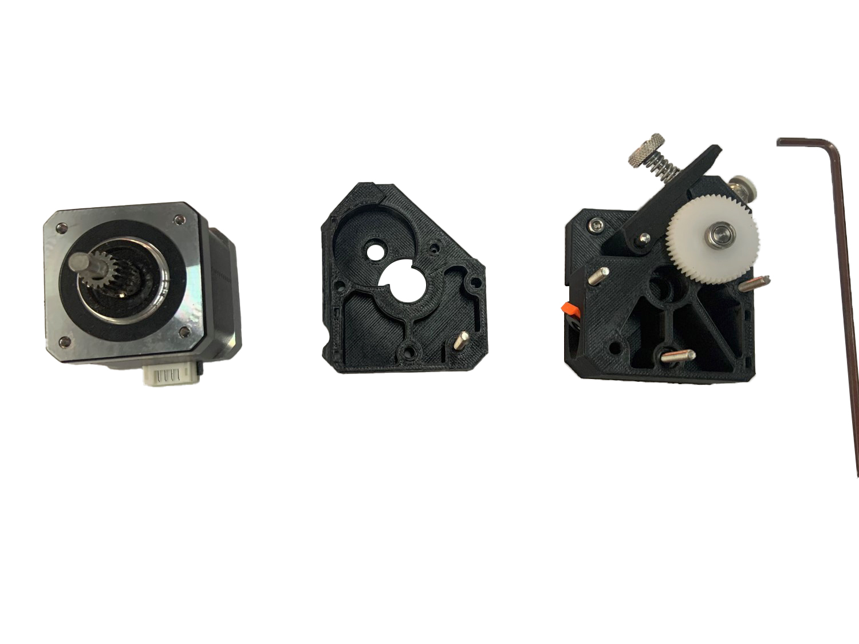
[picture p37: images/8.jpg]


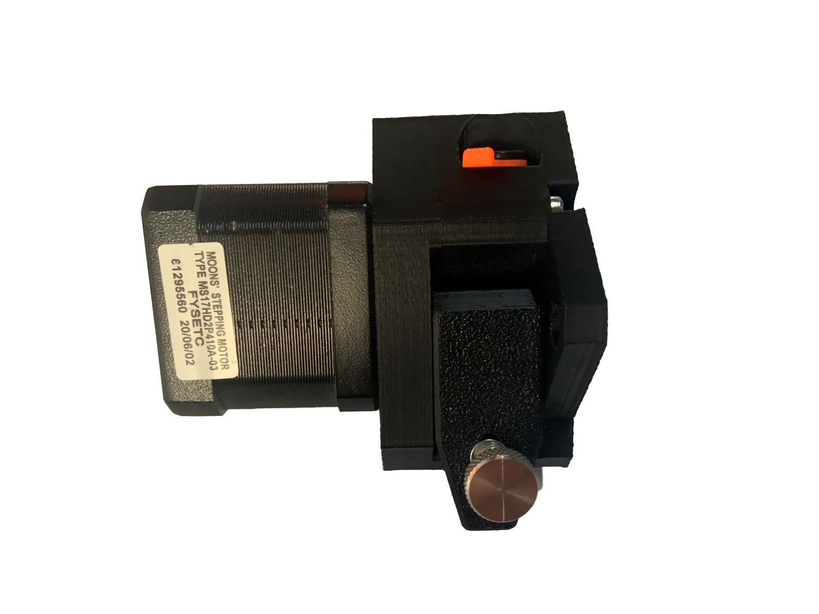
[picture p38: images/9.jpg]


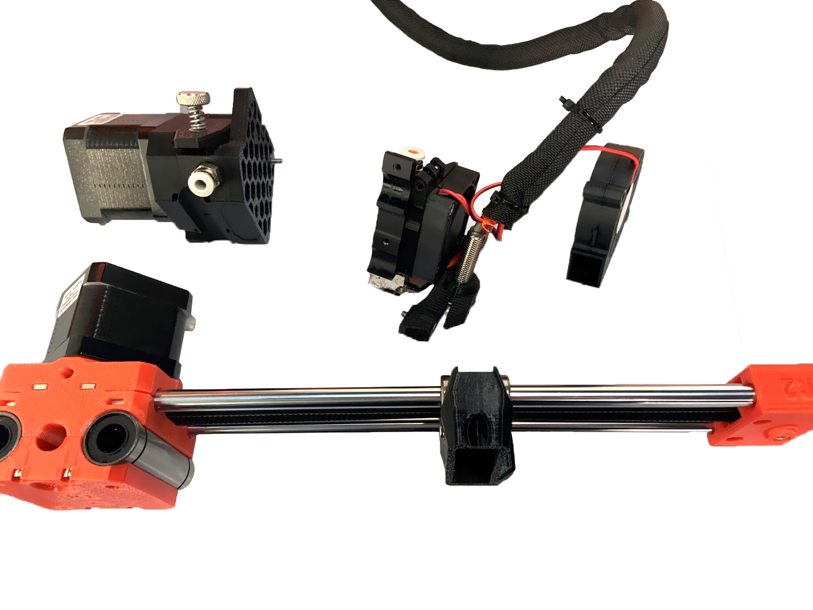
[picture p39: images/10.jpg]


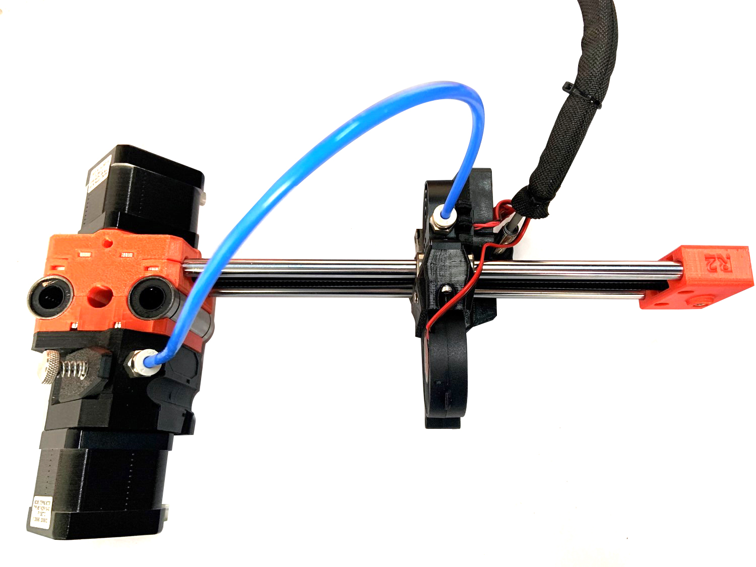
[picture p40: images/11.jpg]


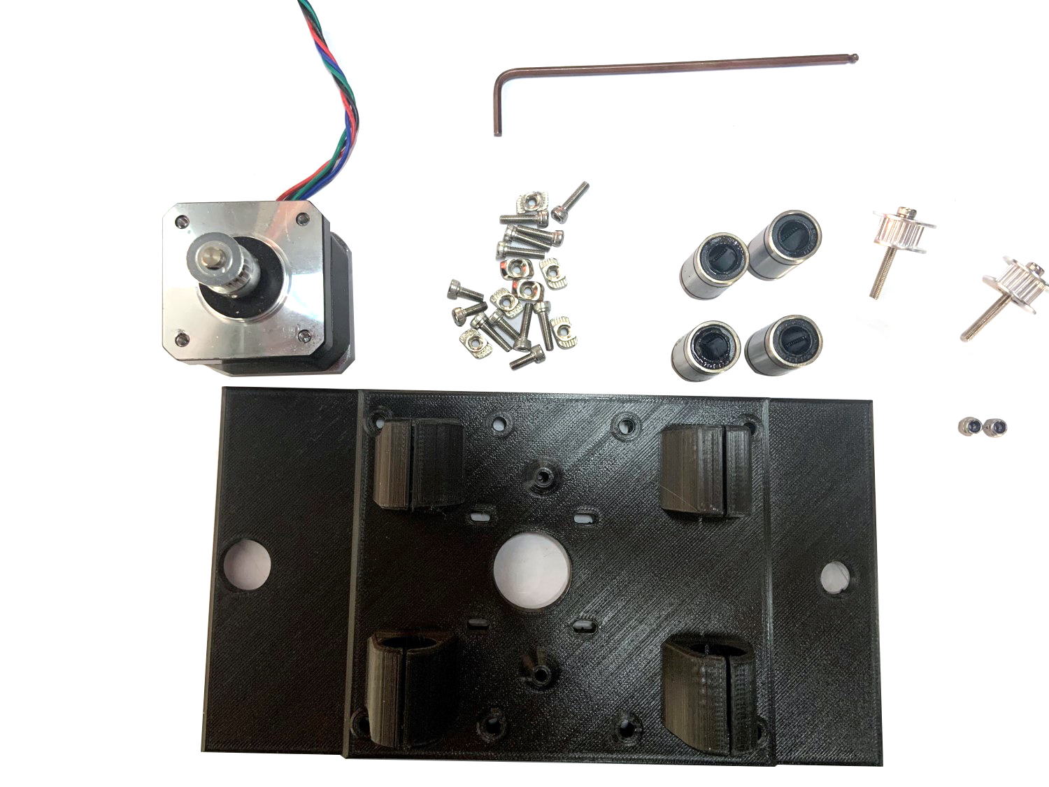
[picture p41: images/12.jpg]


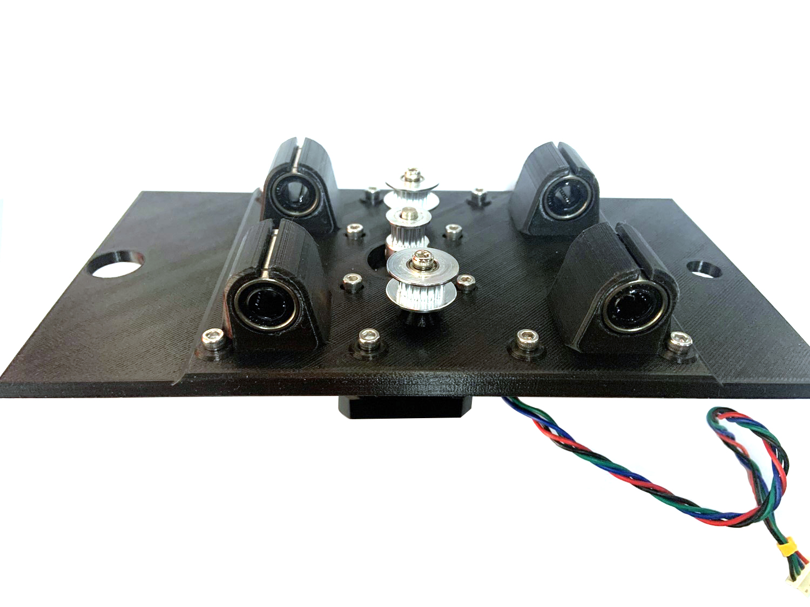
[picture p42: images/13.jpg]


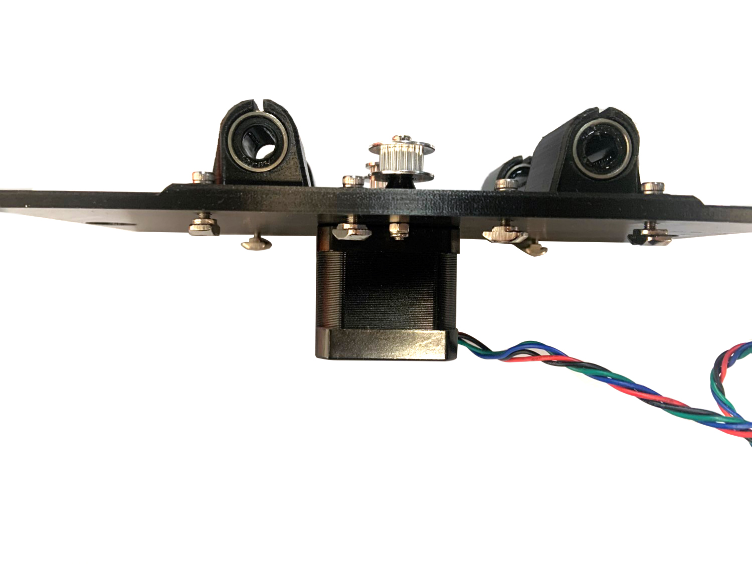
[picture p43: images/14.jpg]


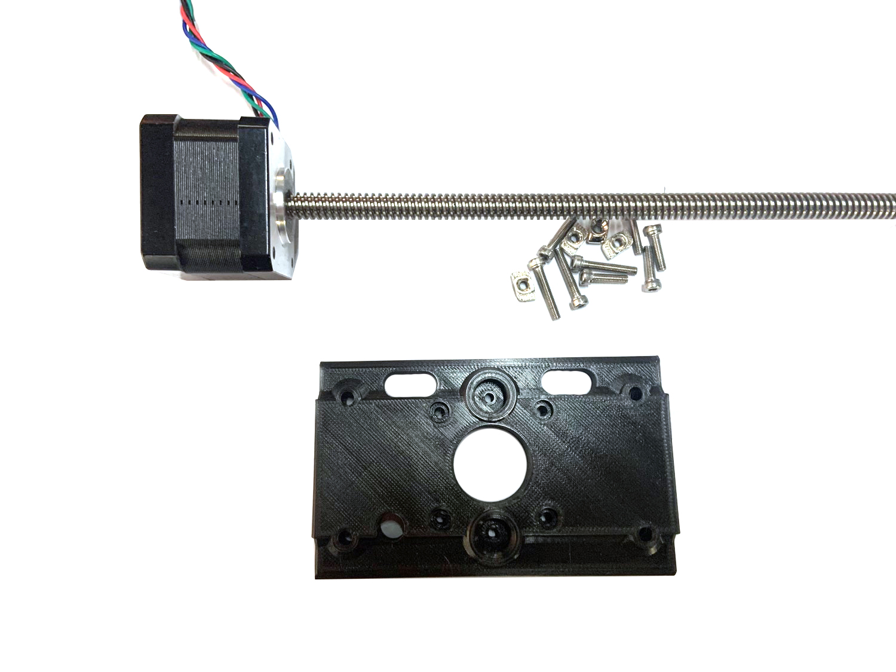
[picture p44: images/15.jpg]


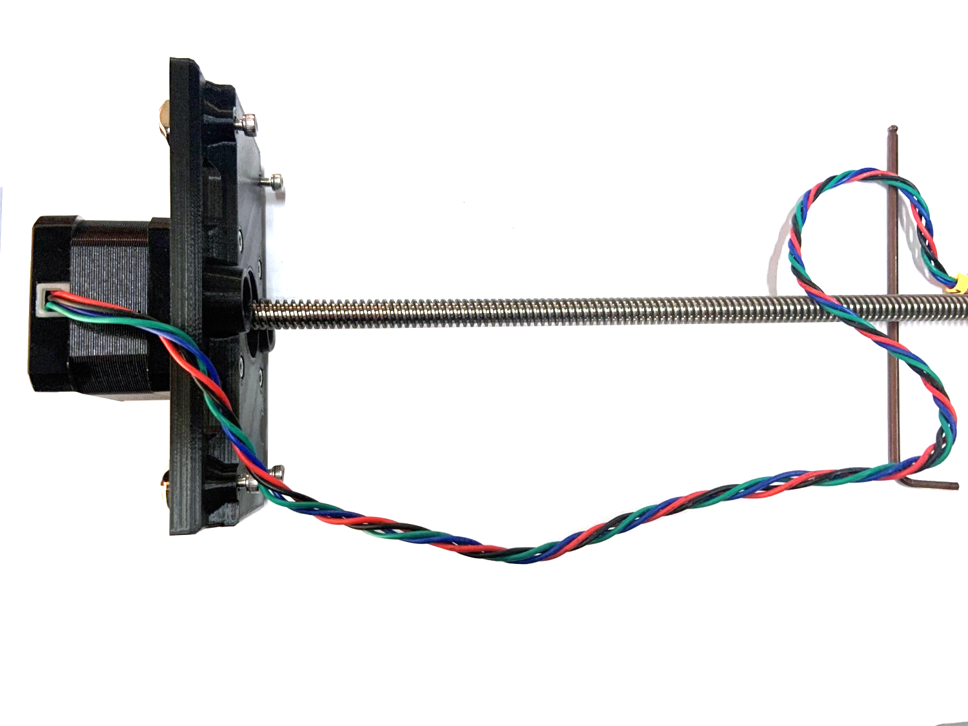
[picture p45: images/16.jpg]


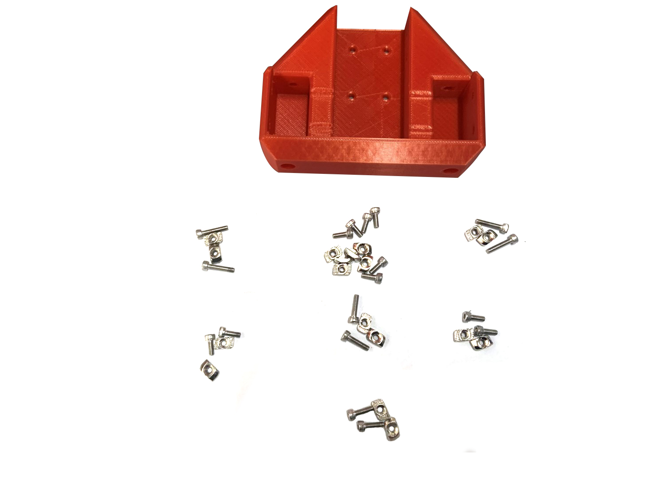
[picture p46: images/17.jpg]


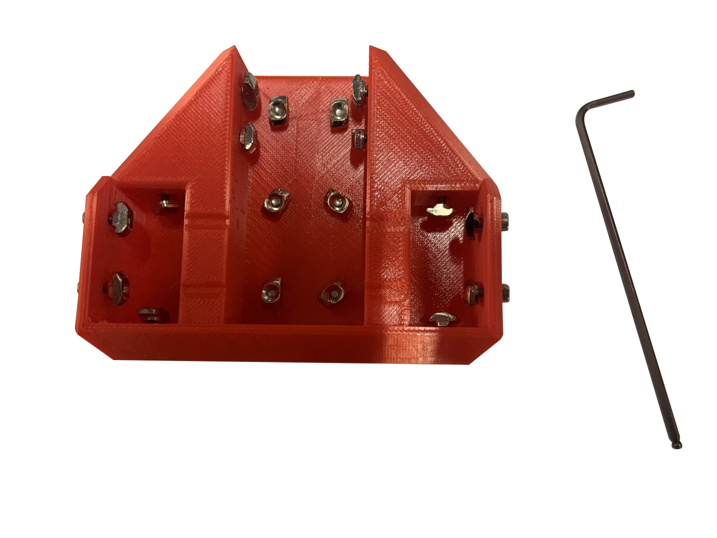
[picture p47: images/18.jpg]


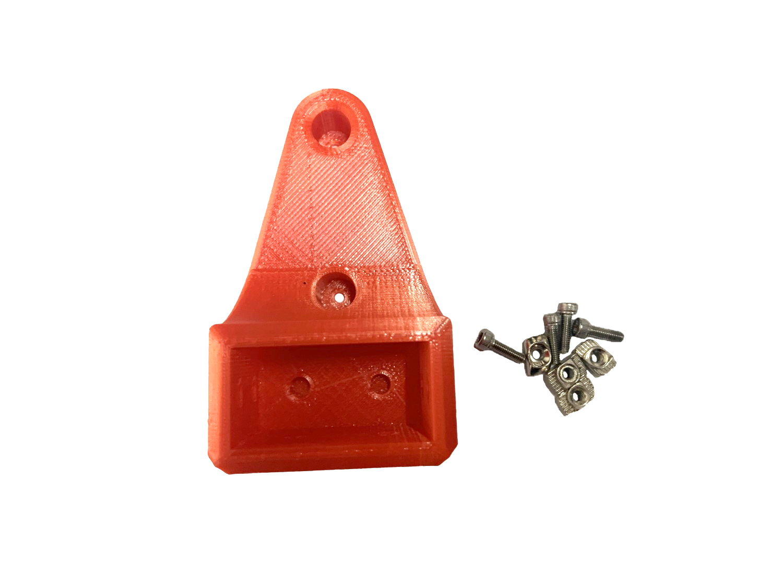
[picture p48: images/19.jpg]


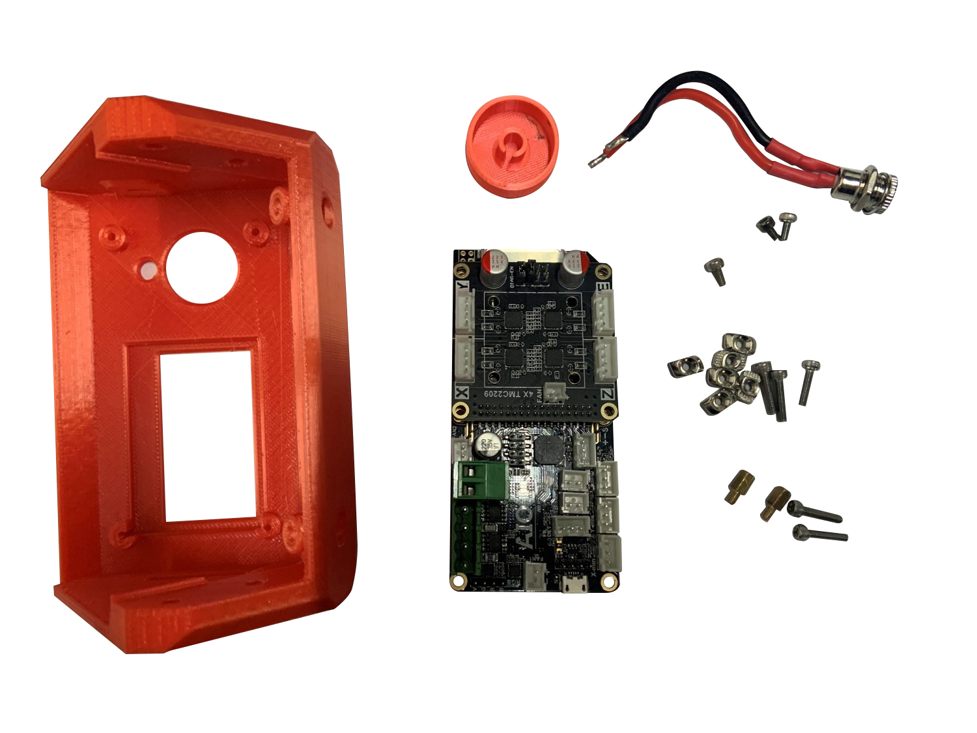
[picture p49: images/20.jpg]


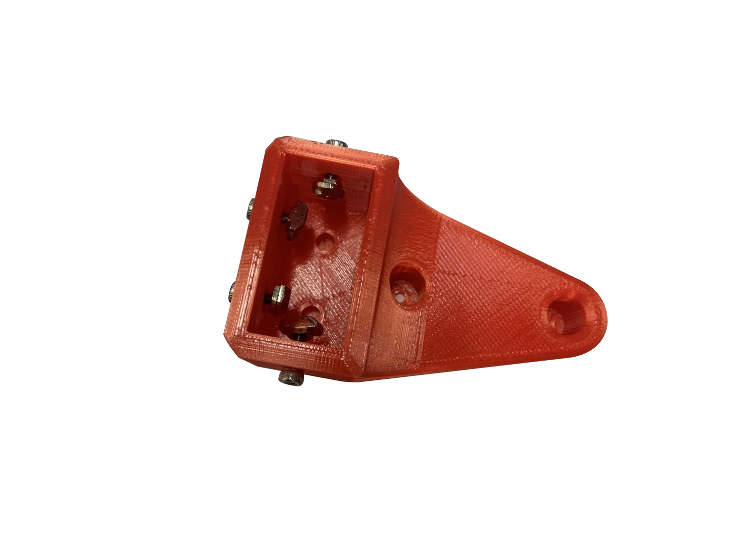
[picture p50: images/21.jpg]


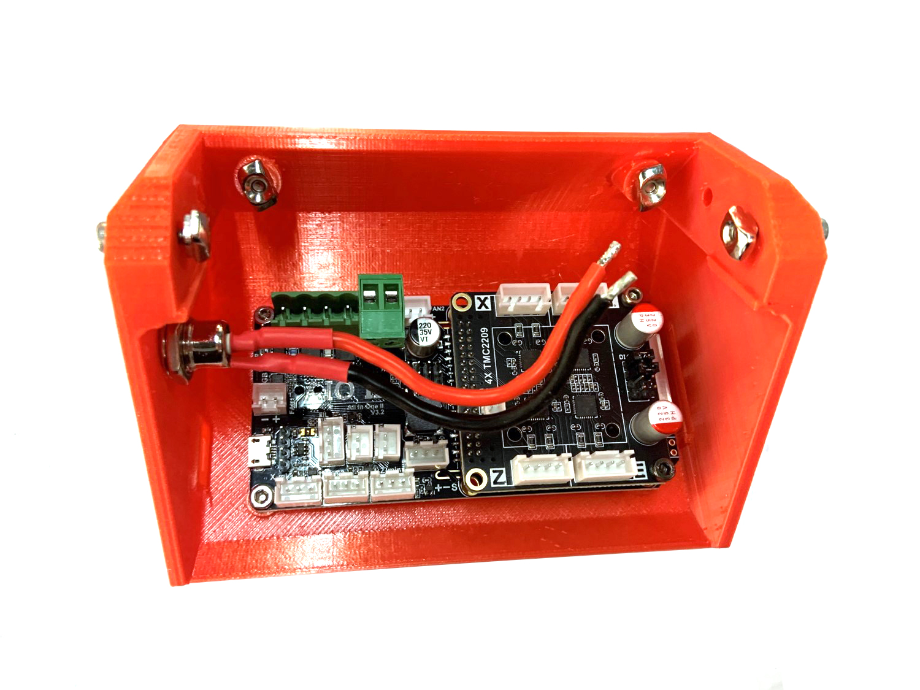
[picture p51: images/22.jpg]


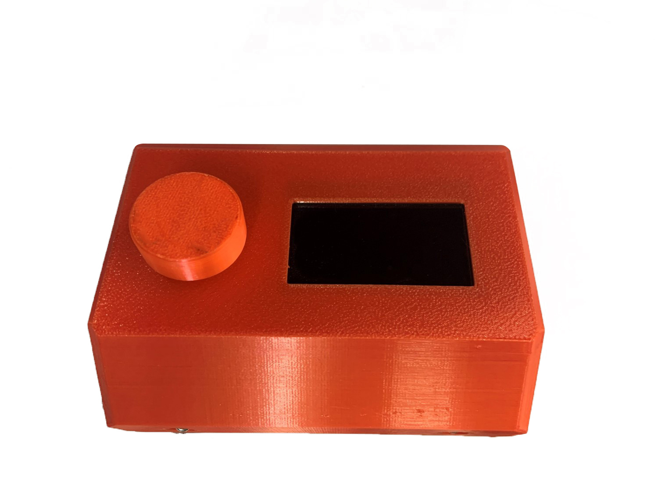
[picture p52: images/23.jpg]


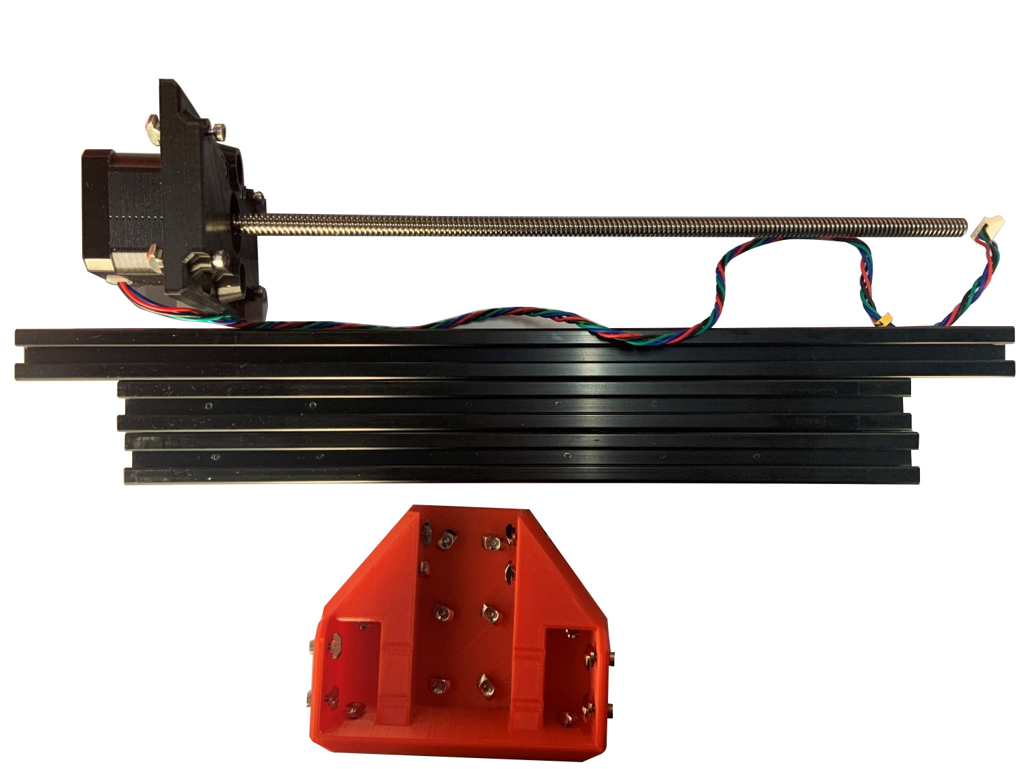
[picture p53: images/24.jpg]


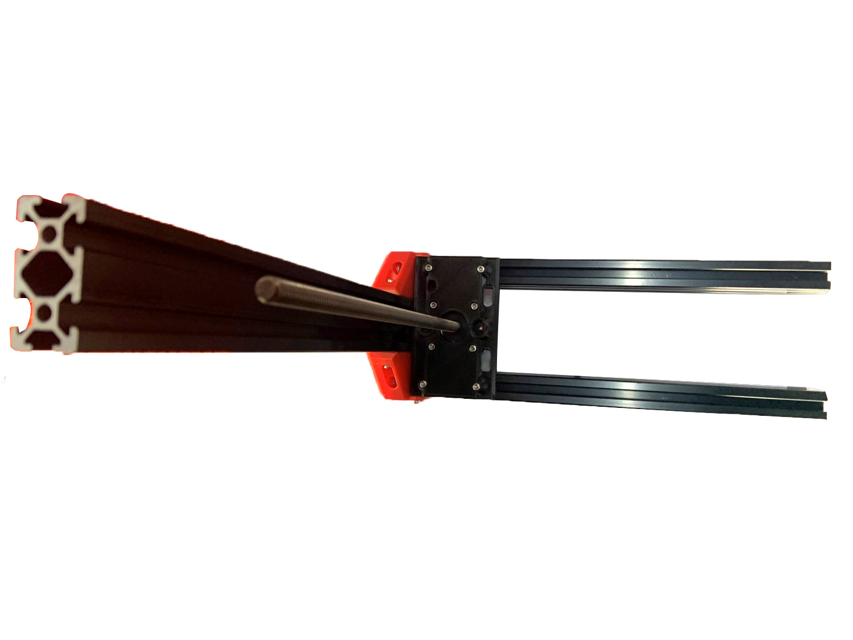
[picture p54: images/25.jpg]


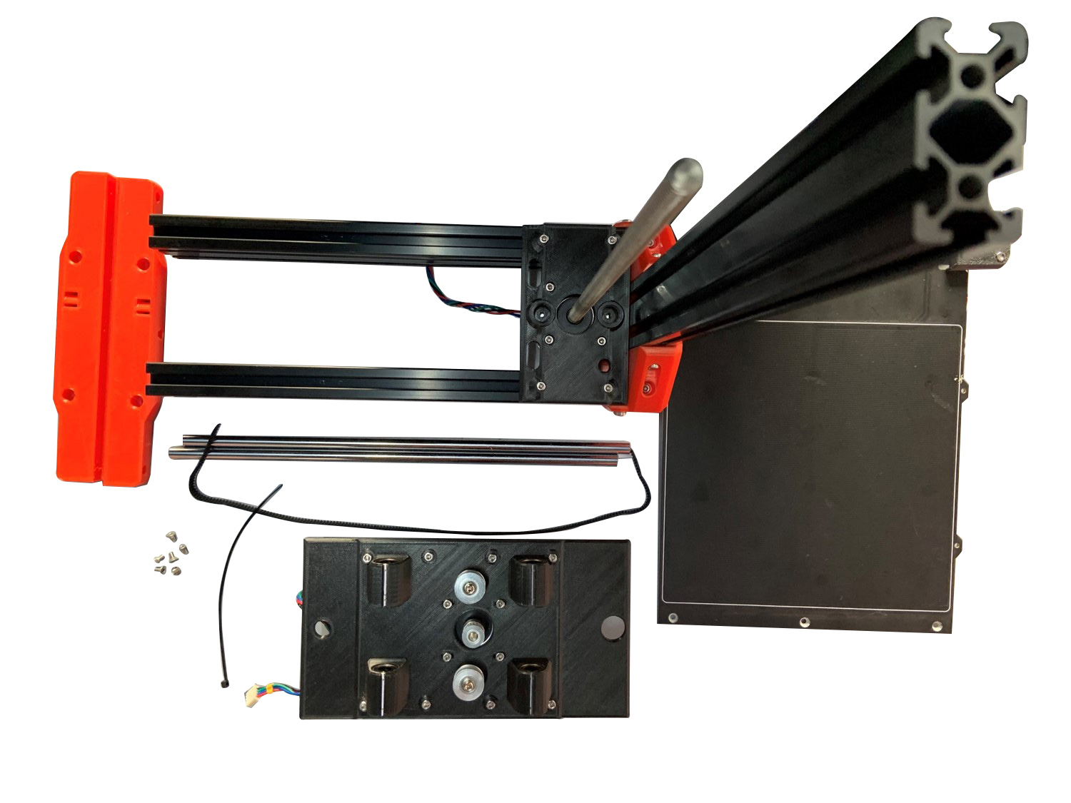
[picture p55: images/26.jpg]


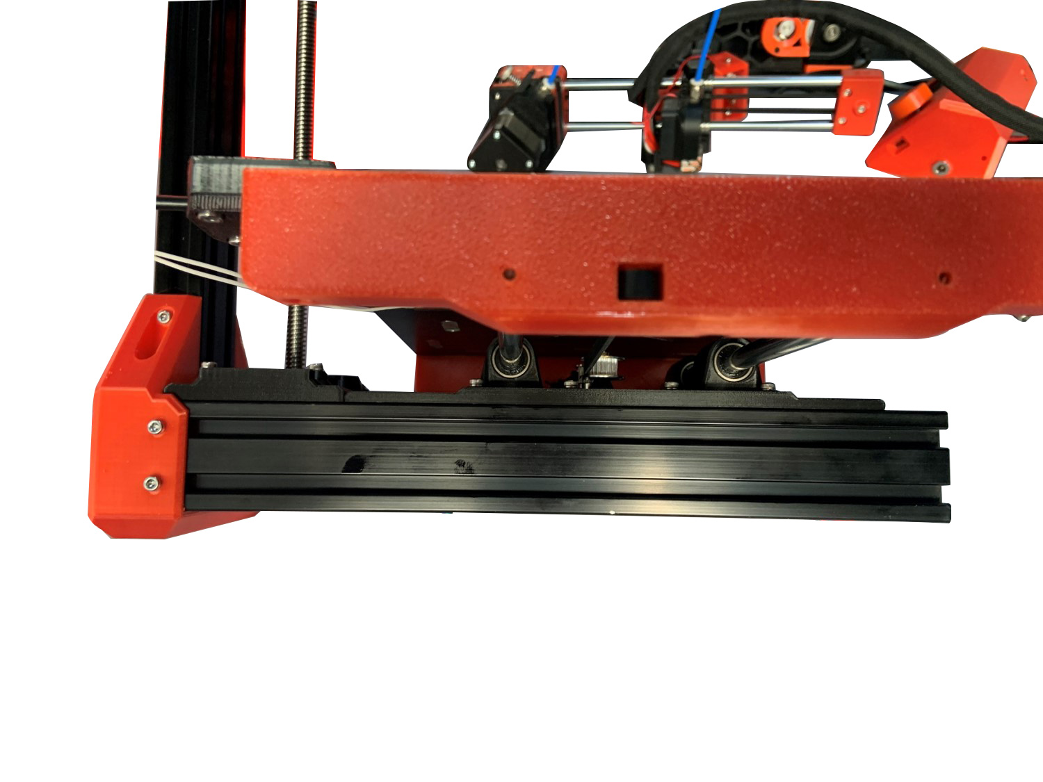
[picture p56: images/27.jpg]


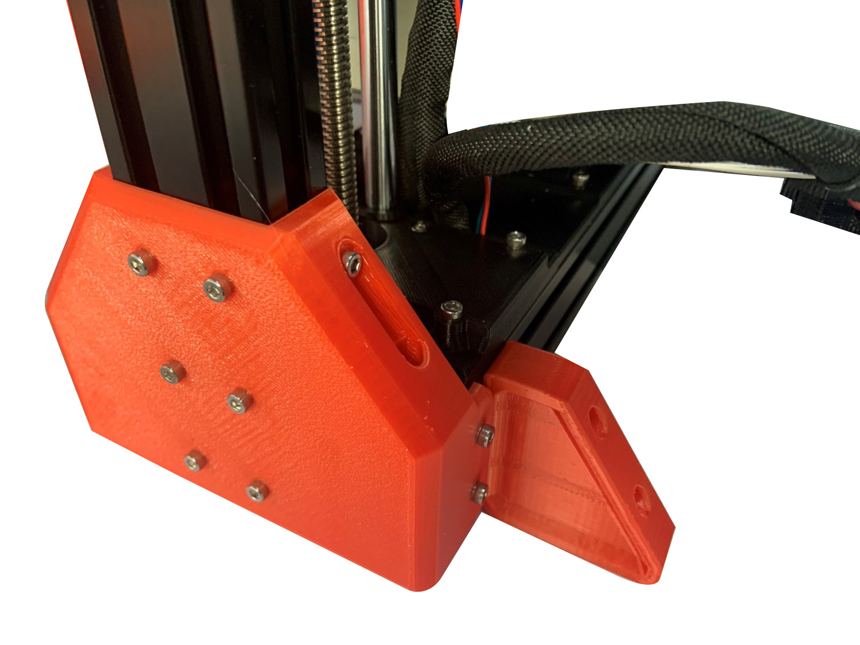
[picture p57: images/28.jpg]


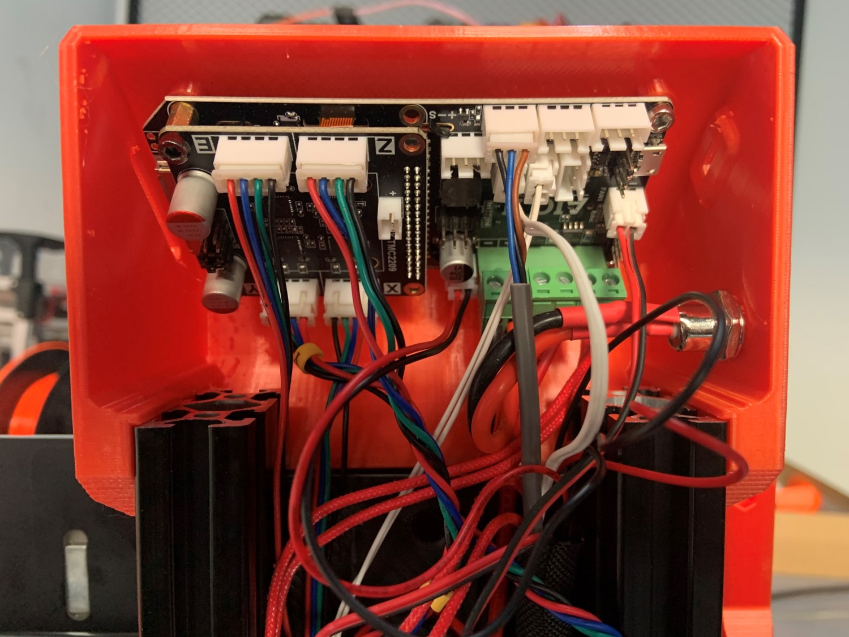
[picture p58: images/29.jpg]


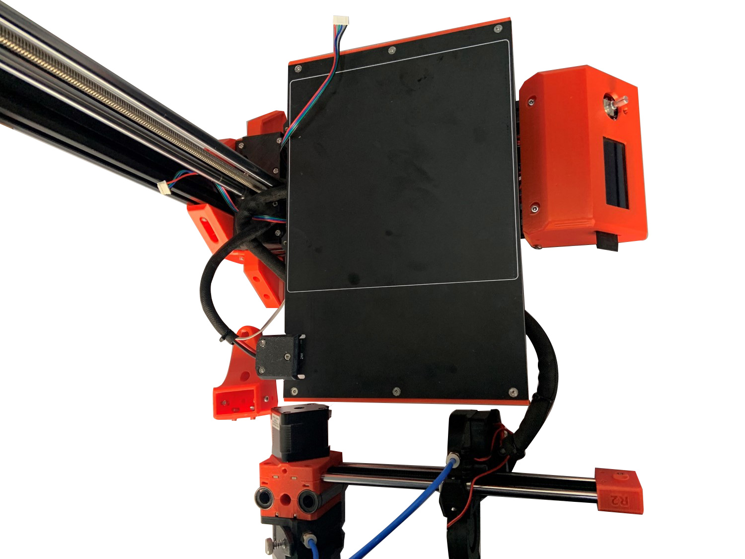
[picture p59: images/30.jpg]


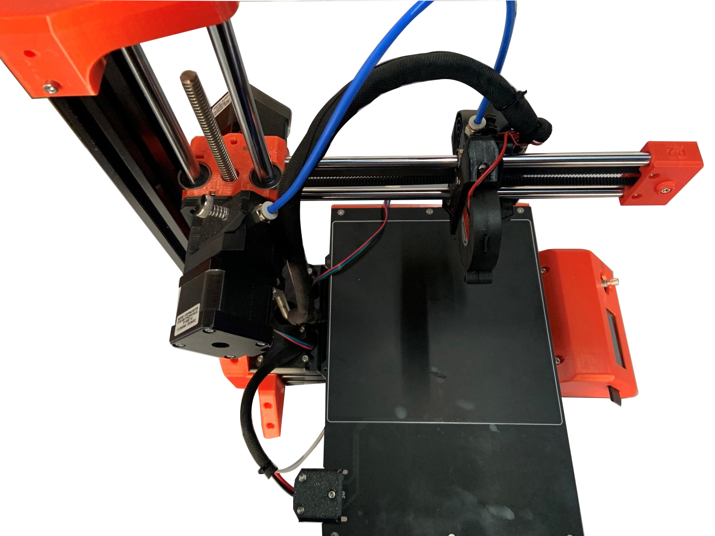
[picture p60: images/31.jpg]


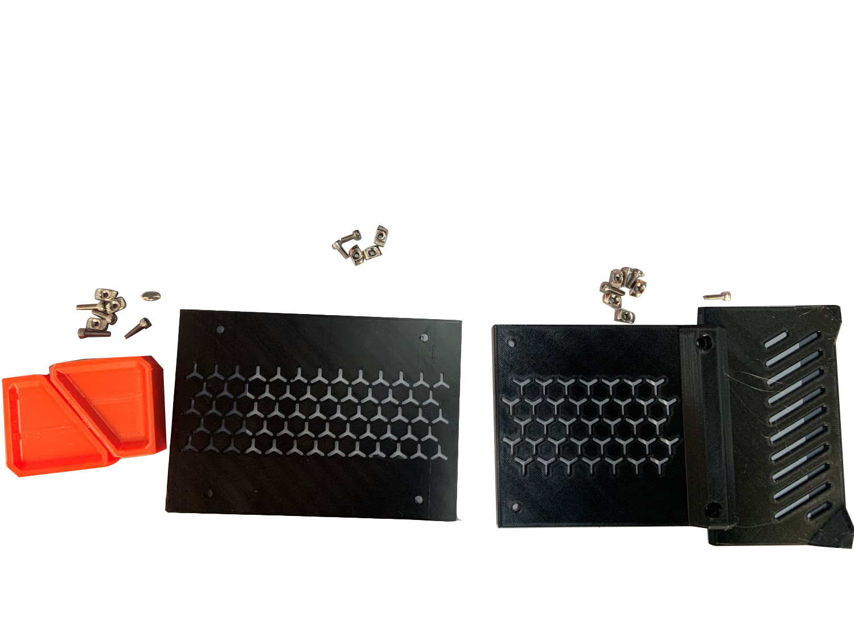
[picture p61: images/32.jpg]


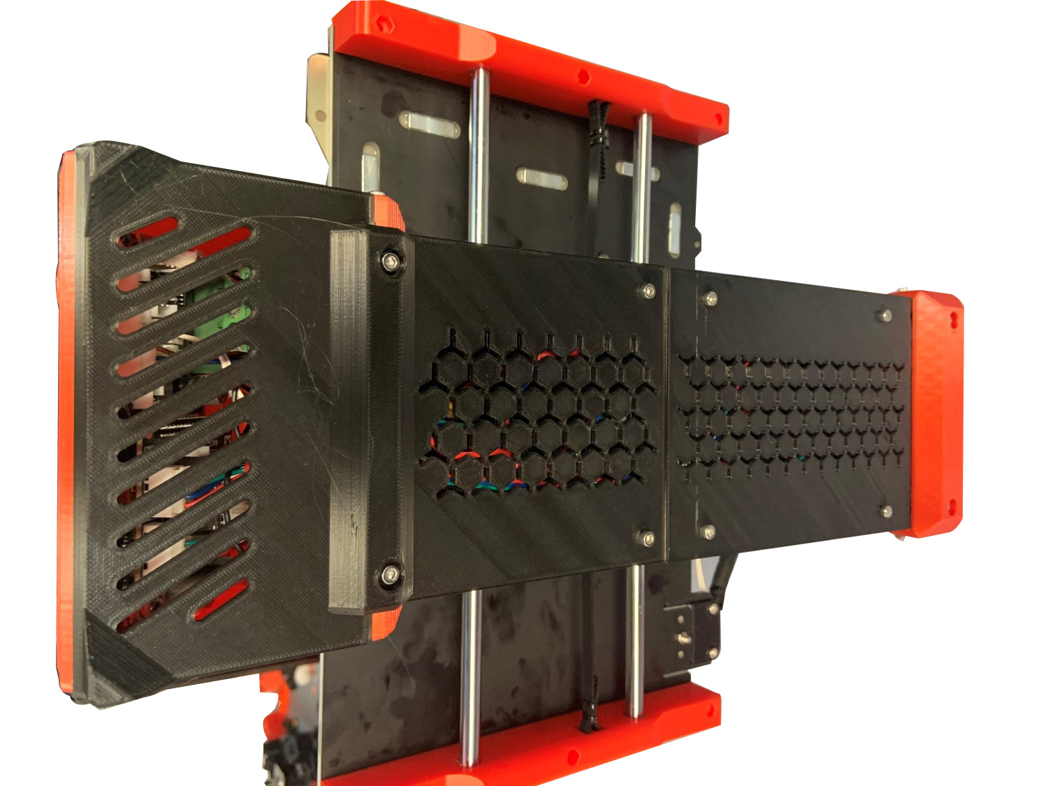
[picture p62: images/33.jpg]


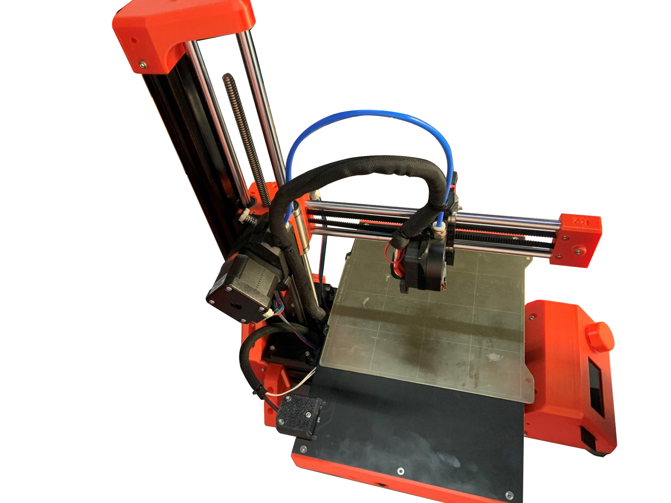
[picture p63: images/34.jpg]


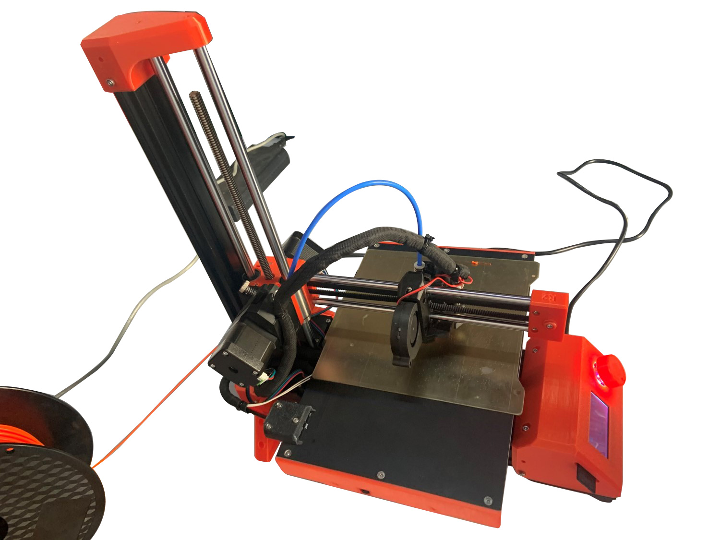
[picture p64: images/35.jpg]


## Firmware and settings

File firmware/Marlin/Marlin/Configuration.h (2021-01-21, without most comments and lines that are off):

#pragma once
#define CONFIGURATION_H_VERSION 020008
#define STRING_CONFIG_H_AUTHOR "(none, default config)" // Who made the changes.
#define SHOW_BOOTSCREEN
#define SERIAL_PORT 1
#define BAUDRATE 115200
  #define MOTHERBOARD BOARD_FYSETC_AIO_II
#define EXTRUDERS 1
#define DEFAULT_NOMINAL_FILAMENT_DIA 1.75
#define TEMP_SENSOR_0 1
#define TEMP_SENSOR_1 0
#define TEMP_SENSOR_2 0
#define TEMP_SENSOR_3 0
#define TEMP_SENSOR_4 0
#define TEMP_SENSOR_5 0
#define TEMP_SENSOR_6 0
#define TEMP_SENSOR_7 0
#define TEMP_SENSOR_BED 0
#define TEMP_SENSOR_PROBE 0
#define TEMP_SENSOR_CHAMBER 0
#define DUMMY_THERMISTOR_998_VALUE 25
#define DUMMY_THERMISTOR_999_VALUE 100
#define MAX_REDUNDANT_TEMP_SENSOR_DIFF 10
#define TEMP_RESIDENCY_TIME     10  // (seconds) Time to wait for hotend to "settle" in M109
#define TEMP_WINDOW              1  // (°C) Temperature proximity for the "temperature reached" timer
#define TEMP_HYSTERESIS          3  // (°C) Temperature proximity considered "close enough" to the target
#define TEMP_BED_RESIDENCY_TIME 10  // (seconds) Time to wait for bed to "settle" in M190
#define TEMP_BED_WINDOW          1  // (°C) Temperature proximity for the "temperature reached" timer
#define TEMP_BED_HYSTERESIS      3  // (°C) Temperature proximity considered "close enough" to the target
#define HEATER_0_MINTEMP   5
#define HEATER_1_MINTEMP   5
#define HEATER_2_MINTEMP   5
#define HEATER_3_MINTEMP   5
#define HEATER_4_MINTEMP   5
#define HEATER_5_MINTEMP   5
#define HEATER_6_MINTEMP   5
#define HEATER_7_MINTEMP   5
#define BED_MINTEMP        5
#define HEATER_0_MAXTEMP 275
#define HEATER_1_MAXTEMP 275
#define HEATER_2_MAXTEMP 275
#define HEATER_3_MAXTEMP 275
#define HEATER_4_MAXTEMP 275
#define HEATER_5_MAXTEMP 275
#define HEATER_6_MAXTEMP 275
#define HEATER_7_MAXTEMP 275
#define BED_MAXTEMP      150
#define PIDTEMP
#define BANG_MAX 255     // Limits current to nozzle while in bang-bang mode; 255=full current
#define PID_MAX BANG_MAX // Limits current to nozzle while PID is active (see PID_FUNCTIONAL_RANGE below); 255=full current
#define PID_K1 0.95      // Smoothing factor within any PID loop
    #define DEFAULT_Kp  22.20
    #define DEFAULT_Ki   1.08
    #define DEFAULT_Kd 114.00
#define MAX_BED_POWER 255 // limits duty cycle to bed; 255=full current
  #define PID_FUNCTIONAL_RANGE 10 // If the temperature difference between the target temperature and the actual temperature
#define PREVENT_COLD_EXTRUSION
#define EXTRUDE_MINTEMP 170
#define PREVENT_LENGTHY_EXTRUDE
#define EXTRUDE_MAXLENGTH 200
#define THERMAL_PROTECTION_HOTENDS // Enable thermal protection for all extruders
#define THERMAL_PROTECTION_BED     // Enable thermal protection for the heated bed
#define THERMAL_PROTECTION_CHAMBER // Enable thermal protection for the heated chamber
#define USE_XMIN_PLUG
#define USE_YMIN_PLUG
#define USE_ZMIN_PLUG
#define ENDSTOPPULLUPS
#define X_MIN_ENDSTOP_INVERTING false // Set to true to invert the logic of the endstop.
#define Y_MIN_ENDSTOP_INVERTING false // Set to true to invert the logic of the endstop.
#define Z_MIN_ENDSTOP_INVERTING false // Set to true to invert the logic of the endstop.
#define X_MAX_ENDSTOP_INVERTING false // Set to true to invert the logic of the endstop.
#define Y_MAX_ENDSTOP_INVERTING false // Set to true to invert the logic of the endstop.
#define Z_MAX_ENDSTOP_INVERTING false // Set to true to invert the logic of the endstop.
#define Z_MIN_PROBE_ENDSTOP_INVERTING false // Set to true to invert the logic of the probe.
#define X_DRIVER_TYPE  TMC2209
#define Y_DRIVER_TYPE  TMC2209
#define Z_DRIVER_TYPE  TMC2209
#define E0_DRIVER_TYPE TMC2209
#define DEFAULT_AXIS_STEPS_PER_UNIT   { 100, 100, 800, 407 }
#define DEFAULT_MAX_FEEDRATE          { 300, 300, 5, 25 }
#define DEFAULT_MAX_ACCELERATION      { 3000, 3000, 100, 10000 }
#define DEFAULT_ACCELERATION          3000    // X, Y, Z and E acceleration for printing moves
#define DEFAULT_RETRACT_ACCELERATION  3000    // E acceleration for retracts
#define DEFAULT_TRAVEL_ACCELERATION   3000    // X, Y, Z acceleration for travel (non printing) moves
#define DEFAULT_EJERK    5.0  // May be used by Linear Advance
  #define JUNCTION_DEVIATION_MM 0.013 // (mm) Distance from real junction edge
  #define JD_HANDLE_SMALL_SEGMENTS    // Use curvature estimation instead of just the junction angle
#define Z_MIN_PROBE_USES_Z_MIN_ENDSTOP_PIN
#define FIX_MOUNTED_PROBE
#define NOZZLE_TO_PROBE_OFFSET { 30, 0, 0 }
#define PROBING_MARGIN 10
#define XY_PROBE_SPEED (133*60)
#define Z_PROBE_SPEED_FAST HOMING_FEEDRATE_Z
#define Z_PROBE_SPEED_SLOW (Z_PROBE_SPEED_FAST / 2)
#define Z_CLEARANCE_DEPLOY_PROBE   10 // Z Clearance for Deploy/Stow
#define Z_CLEARANCE_BETWEEN_PROBES  5 // Z Clearance between probe points
#define Z_CLEARANCE_MULTI_PROBE     5 // Z Clearance between multiple probes
#define Z_PROBE_LOW_POINT         -10 // Farthest distance below the trigger-point to go before stopping
#define Z_PROBE_OFFSET_RANGE_MIN -20
#define Z_PROBE_OFFSET_RANGE_MAX 20
#define X_ENABLE_ON 0
#define Y_ENABLE_ON 0
#define Z_ENABLE_ON 0
#define E_ENABLE_ON 0 // For all extruders
#define DISABLE_X false
#define DISABLE_Y false
#define DISABLE_Z false
#define DISABLE_E false             // Disable the extruder when not stepping
#define DISABLE_INACTIVE_EXTRUDER   // Keep only the active extruder enabled
#define INVERT_X_DIR true
#define INVERT_Y_DIR true
#define INVERT_Z_DIR false
#define INVERT_E0_DIR false
#define INVERT_E1_DIR false
#define INVERT_E2_DIR false
#define INVERT_E3_DIR false
#define INVERT_E4_DIR false
#define INVERT_E5_DIR false
#define INVERT_E6_DIR false
#define INVERT_E7_DIR false
#define X_HOME_DIR -1
#define Y_HOME_DIR -1
#define Z_HOME_DIR -1
#define X_BED_SIZE 180
#define Y_BED_SIZE 180
#define X_MIN_POS 0
#define Y_MIN_POS 0
#define Z_MIN_POS 0
#define X_MAX_POS X_BED_SIZE
#define Y_MAX_POS Y_BED_SIZE
#define Z_MAX_POS 200
#define MIN_SOFTWARE_ENDSTOPS
  #define MIN_SOFTWARE_ENDSTOP_X
  #define MIN_SOFTWARE_ENDSTOP_Y
  #define MIN_SOFTWARE_ENDSTOP_Z
#define MAX_SOFTWARE_ENDSTOPS
  #define MAX_SOFTWARE_ENDSTOP_X
  #define MAX_SOFTWARE_ENDSTOP_Y
  #define MAX_SOFTWARE_ENDSTOP_Z
#define AUTO_BED_LEVELING_BILINEAR
  #define ENABLE_LEVELING_FADE_HEIGHT
  #define SEGMENT_LEVELED_MOVES
  #define LEVELED_SEGMENT_LENGTH 5.0 // (mm) Length of all segments (except the last one)
  #define GRID_MAX_POINTS_X 3
  #define GRID_MAX_POINTS_Y GRID_MAX_POINTS_X
#define MANUAL_Y_HOME_POS -5
#define Z_SAFE_HOMING
  #define Z_SAFE_HOMING_X_POINT 30  // X point for Z homing
  #define Z_SAFE_HOMING_Y_POINT 10  // Y point for Z homing
#define HOMING_FEEDRATE_XY (40*60)
#define HOMING_FEEDRATE_Z  (4*60)
#define VALIDATE_HOMING_ENDSTOPS
#define EEPROM_SETTINGS     // Persistent storage with M500 and M501
#define EEPROM_CHITCHAT       // Give feedback on EEPROM commands. Disable to save PROGMEM.
#define EEPROM_BOOT_SILENT    // Keep M503 quiet and only give errors during first load
#define HOST_KEEPALIVE_FEATURE        // Disable this if your host doesn't like keepalive messages
#define DEFAULT_KEEPALIVE_INTERVAL 2  // Number of seconds between "busy" messages. Set with M113.
#define BUSY_WHILE_HEATING            // Some hosts require "busy" messages even during heating
#define PREHEAT_1_LABEL       "PLA"
#define PREHEAT_1_TEMP_HOTEND 180
#define PREHEAT_1_TEMP_BED     70
#define PREHEAT_1_FAN_SPEED     0 // Value from 0 to 255
#define PREHEAT_2_LABEL       "ABS"
#define PREHEAT_2_TEMP_HOTEND 240
#define PREHEAT_2_TEMP_BED    110
#define PREHEAT_2_FAN_SPEED     0 // Value from 0 to 255
#define PRINTJOB_TIMER_AUTOSTART
#define LCD_LANGUAGE en
#define DISPLAY_CHARSET_HD44780 JAPANESE
#define LCD_INFO_SCREEN_STYLE 0
#define SDSUPPORT
#define FYSETC_MINI_12864_2_0    // Type A/B. Discreet RGB Backlight
#define SOFT_PWM_SCALE 0
#define RGB_LED
  #define PRINTER_EVENT_LEDS
#define SERVO_DELAY { 300 }

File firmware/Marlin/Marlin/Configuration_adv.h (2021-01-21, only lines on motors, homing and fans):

#define E0_AUTO_FAN_PIN -1
#define E1_AUTO_FAN_PIN -1
#define E2_AUTO_FAN_PIN -1
#define E3_AUTO_FAN_PIN -1
#define E4_AUTO_FAN_PIN -1
#define E5_AUTO_FAN_PIN -1
#define E6_AUTO_FAN_PIN -1
#define E7_AUTO_FAN_PIN -1
#define CHAMBER_AUTO_FAN_PIN -1
#define HOMING_BUMP_MM      { 10, 0, 2 }       // (mm) Backoff from endstops after first bump
#define HOMING_BUMP_DIVISOR { 2, 1, 4 }       // Re-Bump Speed Divisor (Divides the Homing Feedrate)
#define MICROSTEP_MODES { 16, 16, 16, 16, 16, 16 } // [1,2,4,8,16]
    #define X_CURRENT       500        // (mA) RMS current. Multiply by 1.414 for peak current.
    #define X_CURRENT_HOME  X_CURRENT  // (mA) RMS current for sensorless homing
    #define X_MICROSTEPS     16    // 0..256
    #define Y_CURRENT       600
    #define Y_CURRENT_HOME  Y_CURRENT
    #define Y_MICROSTEPS     16
    #define Z_CURRENT       300
    #define Z_CURRENT_HOME  Z_CURRENT
    #define Z_MICROSTEPS     16
    #define E0_CURRENT      500
    #define E0_MICROSTEPS    16
  #define X_HYBRID_THRESHOLD     100  // [mm/s]
  #define X2_HYBRID_THRESHOLD    100
  #define Y_HYBRID_THRESHOLD     100
  #define Y2_HYBRID_THRESHOLD    100
  #define Z_HYBRID_THRESHOLD       3
  #define Z2_HYBRID_THRESHOLD      3
  #define Z3_HYBRID_THRESHOLD      3
  #define Z4_HYBRID_THRESHOLD      3
  #define E0_HYBRID_THRESHOLD     30
  #define E1_HYBRID_THRESHOLD     30
  #define E2_HYBRID_THRESHOLD     30
  #define E3_HYBRID_THRESHOLD     30
  #define E4_HYBRID_THRESHOLD     30
  #define E5_HYBRID_THRESHOLD     30
  #define E6_HYBRID_THRESHOLD     30
  #define E7_HYBRID_THRESHOLD     30
  #define SENSORLESS_HOMING // StallGuard capable drivers only
    #define X_STALL_SENSITIVITY  100
    #define X2_STALL_SENSITIVITY X_STALL_SENSITIVITY
    #define Y_STALL_SENSITIVITY  130
    #define Y2_STALL_SENSITIVITY Y_STALL_SENSITIVITY

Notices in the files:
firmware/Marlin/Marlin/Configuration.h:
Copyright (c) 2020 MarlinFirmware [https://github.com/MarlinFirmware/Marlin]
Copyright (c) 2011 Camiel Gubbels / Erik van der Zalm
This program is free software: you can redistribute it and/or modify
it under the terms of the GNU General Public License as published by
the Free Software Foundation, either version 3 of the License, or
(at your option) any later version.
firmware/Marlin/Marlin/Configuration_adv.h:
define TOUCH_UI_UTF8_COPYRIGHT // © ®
